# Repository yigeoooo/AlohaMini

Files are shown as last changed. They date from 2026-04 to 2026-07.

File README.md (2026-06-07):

# AlohaMini2
 

AlohaMini2 is a dual-arm mobile robot with a motorized vertical lift — a major generational upgrade over AlohaMini1 while keeping the self-build BOM under $1,000.  

Fully 3D-printable on a Bambu P2S, built for embodied AI research, and priced for anyone serious about real-world manipulation.

> Assemble at home in ~120 minutes. Train or deploy with LeRobot.

## Updates

- [2026-06-06] AlohaMini2 released — 70 kg base load, 30 kg lift, 1 kg arm payload, 6+1 DoF, 52 cm reach, under $1,000 self-build BOM
- [2026-02-26] Fine-tuning and deployment guide for Pi 0.5 on AlohaMini (`examples/pi0.5_openpi`)
- [2025-12-18] URDF and simulation assets available (`AlohaMini1/simulation/src/Aloha/`)
- [2025-11-27] STEP (CAD) files available (`AlohaMini1/hardware/mobile_base/step/`)

## What's New in AlohaMini2

### Architecture

| | AlohaMini | AlohaMini2 |
|---|---|---|
| Arm system | [SO-ARM100 / SO-ARM101](https://github.com/TheRobotStudio/SO-ARM100) | [AM-ARM200](https://github.com/liyiteng/AM-ARM) |
| Mobile base system | [mobile_base1](AlohaMini1/hardware/mobile_base/) | [mobile_base2](AlohaMini2/hardware/mobile_base2/) |
| Printer requirement | Large-format FDM (>= 380 mm bed) | Bambu P2S (consumer-grade) |

### Performance

| | AlohaMini | AlohaMini2 |
|---|---|---|
| Base max load | 10 kg | 70 kg  |
| Lift capacity | 5 kg | 30 kg |
| Lift stability | Standard | Significantly reinforced |
| Arm payload | 0.3 kg | 1 kg |
| Arm reach | 40 cm | 52 cm |
| Arm DoF | 5+1 | 6+1 |
| Cameras | 5 | 5 (forward, backward, chest, dual wrist) |

AlohaMini2 is LeRobot-ready out of the box and remains fully open-source — hardware CAD, URDF, and software included.

## Gallery

<p align="center">
  
</p>

## Bill of Materials (BOM)

> This BOM lists only the robot's major components, excluding the leader arm.

| Component | Model / Notes | Qty | Unit Price (USD) |
|---|---|-----|---|
| Servo — standard | Feetech STS-3215 (12V, follower arms + base) | 11 | ~$16 |
| Servo — high-torque | Feetech STS-3095 (12V 95 kg·cm, lift + arm power joints) | 7 | ~$50 |
| Bus servo controllers | Waveshare | 2 | ~$5 |
| Compute | Raspberry Pi 5 (2 GB) | 1 | ~$93 |
| Cameras | 720p USB, 2.4 mm focal length | 5 | ~$17 |
| Omni wheels | 127 mm (74A) | 3 | ~$40 |
| Battery 12V | 11200 mAh Li-ion | 2 | ~$16 |
| Frame | 3D-printed on Bambu P2S | — | ~6 kg filament |
| **Total** | — | — | **~$950** |

> Full BOM with CN/US buy links: **[AlohaMini2/docs/BOM.md](AlohaMini2/docs/BOM.md)**  
> Compute can be swapped for Jetson Orin Nano or any SBC with USB 3.0.  

## Quick Start

1. **BOM** — review the component list and source parts  
   See **[Bill of Materials](AlohaMini2/docs/BOM.md)**

2. **3D Printing** — print all structural parts (~6 kg filament, Bambu P2S)  
   See **[Print Guide](AlohaMini2/docs/print_guide.md)**

3. **Assembly** — build in ~120 minutes (arms pre-assembled)  
   See **[Assembly Guide](AlohaMini2/docs/assembly_guide.md)**

4. **Software setup & teleoperation** — install, connect, control  
   See **[Software Guide](software)**

## Product Line

| Model | Servo System | Chassis | Best For | Official Store (CN) |
|---|---|---|---|---|
| **AlohaMini2** | STS-3215 standard servos | 3D-printed base | Self-build research and development | [Taobao](https://item.taobao.com/item.htm?abbucket=9&id=1015799132286) |
| **AlohaMini2 Pro** | STS-3250 industrial-grade servos | Metal-reinforced base | Higher-duty research and lab use | [Taobao](https://item.taobao.com/item.htm?abbucket=9&id=1015799132286) |

## Contact

Email: liyiteng+github@gmail.com  
WeChat: liyiteng  
Videos & tutorials: Bilibili / YouTube / TikTok

## Team

AlohaMini is created by **Li Yiteng** and **Wu Zhiyong**.

## Acknowledgements

Thanks to the open robotics community:  
**ALOHA · LeKiwi · SO-ARM100 · SO-ARM100-Track-Axis · Pi-0.5 · LeRobot · Hugging Face**

## Support AlohaMini

If you find this project useful:
- Star the repo
- Follow for updates
- Join the community on Discord

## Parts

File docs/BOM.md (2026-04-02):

# Bill of Materials

AlohaMini follows the same architecture and terminology as LeKiwi, consisting of a Client side and a Host side.

- The Client handles computation and control.
- The Host executes commands and returns observations.

This is also commonly referred to as PC side vs. Remote side, and both naming conventions are equivalent.

AlohaMini’s Client hardware includes the mobile base and two follower arms. The arms directly reuse the SO-ARM100 design. Therefore, if you already have two SO-ARM100 arms, you only need to assemble the mobile base. Communication between the mobile base, arms, and Raspberry Pi 5 uses the same bus-servo communication system, and the build guide will explain the wiring in detail.

On AlohaMini, the Host side consists of a PC workstation and leader arms. VR controllers or other devices can also replace the leader arms, and we will release compatible controller kits soon. For beginners, we recommend starting with leader-arm teleoperation.

*Note: Table clamp, screwdriver set, soldering iron, and other common tools can be sourced as needed and are not listed in the tables below.*

## Mobile base 

| Item | Model / Notes | Qty | Unit Cost (US) | Buy (US) | Unit Cost (CN) | Buy (CN) |
|---|---|-----|---|---|---|---|
| Servo motor | Feetech / 12V 1/345 Gear(STS3215-C018)| 4 | $13.89 | [Alibaba](https://www.alibaba.com/product-detail/Feetech-12V-1-345-STS3215-C018_1601637205886.html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) | ¥110 | [taobao](https://item.taobao.com/item.htm?id=996544351583&spm=a213gs.v2success.0.0.73c04831naDrHP) |
| Omni wheel | 4″ (≈100 mm) | 3 | $47 | [Amazon](https://www.amazon.com/Replacement-Plastic-Directional-Accessories-Platform/dp/B0F9W6QX5M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) | ¥135 | [pinduoduo](https://mobile.yangkeduo.com/goods.html?ps=kKWPC7xuzw) |
| USB camera | 720p focal length 2.4 mm, 36×36 mm form factor | 3 | — | Amazon | ¥125 | [taobao](https://item.taobao.com/item.htm?id=666278411821) |
| (optional) Bearing | 12×18×4 mm (ID × OD × W) — wheel axle bearing | 3 | — | Amazon | ¥6 | [tmall](https://detail.tmall.com/item.htm?id=824704356695) |
| Bearing | 4×13×5 mm (ID × OD × W) — lift axis bearing | 8 | — | Amazon | ¥3 | [taobao](https://item.taobao.com/item.htm?id=565418362178) |
| M2×12 Phillips screw | For camera mounts (OB_T_Camera_Mount.stl, OB_Top_Camera_Mount) | 12 | — | — | — | — |
| M3×12 hex socket screw | Total 36 pcs (Servo Mount×24 ,Side Panel×12 ) | 36 | — | — | — | — |
| M3×18 hex socket screw | For OB_Chassis_Wheel_Axle_Connector.stl | 12 | — | — | — | — |
| M3×30 hex socket screw | For OB_T_Connector_Right/Left.stl | 8 | — | — | — | — |
| M3 hex nut | For OB_T_Connector_Right/Left.stl | 8 | — | — | — | — |
| M3x5x4 heat-set insert | Total 36 pcs (Servo Mount×24, Side Panel×12) | 36 | — | Amazon | ¥5 | [taobao](https://item.taobao.com/item.htm?id=809241671998) |
| M4×12 hex socket screw | Total 20 pcs (Bearing Cover×12, Z-axis Servo Mount×8) | 20 | — | Amazon | — | — |
| M4x6x5 heat-set insert | For OB_Chassis_Bearing_Cover.stl | 12 | — | Amazon | ¥4 | [taobao](https://item.taobao.com/item.htm?id=809241671998) |
| Adhesive | Epoxy (strongly recommended) / double-sided tape — cable retention & structural bonding | 1 | — | Amazon | ¥12 | [jd](https://item.jd.com/100141557259.html) |
| Servo extension cable | SCS 3-pin, 90 cm | 2 | — | [Alibaba](https://www.alibaba.com/product-detail/3P-5264-Interface-Bus-Actuator-Connection_1601635790774.html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) | ¥3 | [taobao](https://item.taobao.com/item.htm?id=616460581906) |
| Battery | 12 V Li-ion pack with 5521 barrel jack (male & female); one pack for the Raspberry Pi 5, the other for the mobile base and follower arms.| 2 | $43 | [Amazon](https://www.amazon.com/KBT-Rechargeable-Connector-Replacement-Security/dp/B0C242DYT1/ref=sr_1_2_sspa?th=1) | ¥130 | [taobao](https://item.taobao.com/item.htm?id=890828103056) |
| USB Type-C cable | Only for testing the mobile base | 1 | $10 | [Amazon](https://www.amazon.com/Charging-etguuds-Charger-Braided-Compatible/dp/B0B8NWLLW2/?th=1) | ¥20 | [tmall](https://detail.tmall.com/item.htm?id=754024805047) |
| Waveshare Bus Servo Controller | Only for testing the mobile base | 1 | $13 | [Amazon](https://www.amazon.com/Waveshare-Integrates-Control-Circuit-Supports/dp/B0CTMM4LWK/) | ¥27 | [tmall](https://detail.tmall.com/item.htm?id=738817173460) |
| 3D-printed parts | PLA/PETG/ABS (files in /hardware/mobile_base/stl) | ~4 kg filament | — | — | — | — |

**3D Printing Parts List:**
- OB_Chassis_Bearing_Cover x3
- OB_Chassis_Servo_Mount x3
- OB_Chassis_Side_Panel x3
- OB_Chassis_Wheel_Axle_Connector x3
- OB_Chassis_Wheel_Guard x3
- OB_Top_Camera_Back_Cover x2
- OB_Chassis_Shaft_Sleeve_12_24 x3
- O_Chassis_Dowel_Pin_12_37 x3
- All other files x1

Note：
All other parts — including the lift mechanism — can be printed on a standard 3D printer. Only the chassis is special, as it requires a build volume of at least 385 × 345 × 64 mm. We recommend choosing a machine with around 400 × 360 × 100 mm or larger. Due to its size, the chassis may need to be outsourced for printing.

### What the Base Can Do

With only the components above, you can assemble the **mobile base** and control:

- movement  
- vertical lift  

Use the following commands to control the base:
```bash
python examples/debug/wheels.py \
   --port /dev/ttyACM0

python examples/debug/axis.py \
   --port /dev/ttyACM0
```

Use W/S/A/D to drive the base, and U/J to raise or lower the lift — all directly from your PC, without installing any single-board computer on the robot.

More details will be provided in the software setup section.

Effect after assembly:

Assembled AlohaMini mobile base
### Standalone Mode (Optional)

If you prefer the base to operate as an **independent host system** (Wi‑Fi, untethered), add:

| Item | Model / Notes | Qty | Unit Cost (US) | Buy (US) | Unit Cost (CN) | Buy (CN) |
|---|---|-----|---|---|---|---|
| Compute board | Raspberry Pi 5 (≥ 2GB RAM) | 1 | $80 | [Adafruit](https://www.adafruit.com/product/5812) | ¥600 | [taobao](https://item.taobao.com/item.htm?id=688878446695) |
| DC converter | 12V → 5V / 5A buck converter | 1 | $13 | [Amazon](https://www.amazon.com/Klnuoxj-Converter-Interface-Waterproof-Compatible/dp/B0CRVW7N2J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) | ¥75 | [taobao](https://item.taobao.com/item.htm?id=800698078303) |
| Monitor | 7-inch HD IPS HDMI interface + touch + Type C power supply | 1 | — | Amazon | ¥291 | [taobao](https://item.taobao.com/item.htm?id=592070943040) |

## Follower Arms
| Item | Model / Notes | Qty | Unit Cost (US) | Buy (US) | Unit Cost (CN) | Buy (CN) |
|---|---|-----|---|---|---|---|
| Servo motor | Feetech / 12V 1/345 Gear(STS3215-C018) | 12 | $13.89 | [Alibaba](https://www.alibaba.com/product-detail/Feetech-12V-1-345-STS3215-C018_1601637205886.html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) | ¥110 | [taobao](https://item.taobao.com/item.htm?id=996544351583&spm=a213gs.v2success.0.0.73c04831naDrHP) |
| Waveshare Bus Servo Controller | For connecting to the Raspberry Pi 5 | 2 | $13 | [Amazon](amazon.com/Waveshare-Integrates-Control-Circuit-Supports/dp/B0CTMM4LWK/) | ¥27 | [tmall](https://detail.tmall.com/item.htm?id=738817173460) |
| USB camera | 720p focal length 3.8 mm, 32×32 mm form factor | 2 | — | Amazon | ¥103 | [taobao](https://item.taobao.com/item.htm?id=590682120464) |
| 1-to-2 DC splitter cable | 30 cm, 5521 connector — for powering the arms | 1 | — | Amazon | ¥5 | [taobao](https://item.taobao.com/item.htm?id=594921965049) |
| DC extension cable | 1.5 m, 5521 connector — for powering the arms | 2 | — | Amazon | ¥2.50 | [taobao](https://item.taobao.com/item.htm?id=43628177900) |
| USB Type-C cable | For connecting to the Raspberry Pi 5 | 2 | $10 | [Amazon](https://www.amazon.com/Charging-etguuds-Charger-Braided-Compatible/dp/B0B8NWLLW2/?th=1) | ¥20 | [tmall](https://detail.tmall.com/item.htm?id=754024805047) |
| 3D-printed parts | PLA/PETG/ABS (files in /hardware/arms/stl) | 1 set | — | — | — | — |

**3D Printing Parts List:**
- All "D_*.stl" files: x2
- All "F_*.stl" files: x2

For detailed printing instructions, refer to the [SO-ARM100 project README](https://github.com/TheRobotStudio/SO-ARM100)

## Leader Arms
> **Note:** The official SO-ARM100 design uses three different gear ratios (1/147, 1/191, 1/345) for optimal performance. However, our testing shows that using a single gear ratio (1/147) provides excellent user experience and significantly simplifies assembly. The BOM below reflects this simplified configuration.

| Item | Model / Notes | Qty | Unit Cost (US) | Buy (US) | Unit Cost (CN) | Buy (CN) |
|---|---|-----|---|---|---|---|
| Servo motor | Feetech / 7.4V 1/147 Gear(STS3215-C046) | 12 | $13.89 | [Alibaba](https://www.alibaba.com/product-detail/Feetech-STS3215-Servos-Feetech-7-4V_1601636218844.html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) | ¥99 | [taobao](https://item.taobao.com/item.htm?id=996544351583&spm=a213gs.v2success.0.0.73c04831naDrHP) |
| Waveshare Bus Servo Controller | For connecting to the PC | 2 | $13 | [Amazon](https://www.amazon.com/Waveshare-Integrates-Control-Circuit-Supports/dp/B0CTMM4LWK/) | ¥27 | [tmall](https://detail.tmall.com/item.htm?id=738817173460) |
| Battery | 5V Li-ion pack (5600mAh, DC 5521 connector) | 1 | — | Amazon | ¥30 | [taobao](https://item.taobao.com/item.htm?id=765749120668) |
| 1-to-2 DC splitter cable | 70 cm — for powering the arms | 1 | — | Amazon | ¥5 | [taobao](https://item.taobao.com/item.htm?id=594921965049) |
| USB Type-C cable | For connecting to the PC | 2 | $10 | [Amazon](https://www.amazon.com/Charging-etguuds-Charger-Braided-Compatible/dp/B0B8NWLLW2/?th=1) | ¥20 | [tmall](https://detail.tmall.com/item.htm?id=754024805047) |
| 3D-printed parts | PLA/PETG/ABS (files in /hardware/arms/stl) | 1 set | — | — | — | — |

**3D Printing Parts List:**
- All "D_*.stl" files: x2
- All "L_*.stl" files: x2

For detailed printing instructions, refer to the [SO-ARM100 project README](https://github.com/TheRobotStudio/SO-ARM100)

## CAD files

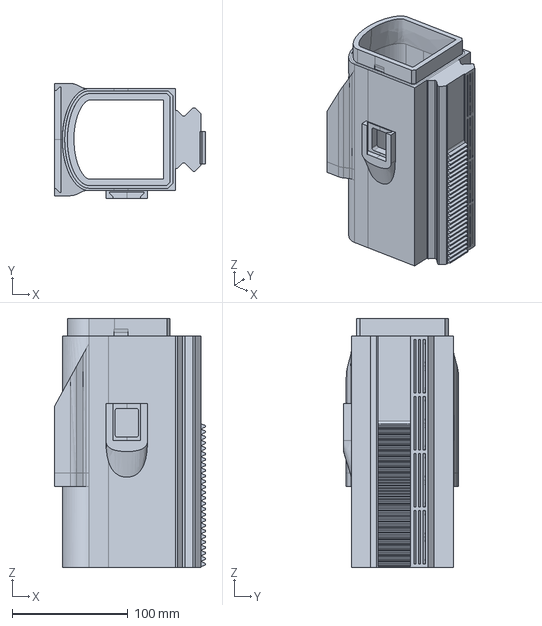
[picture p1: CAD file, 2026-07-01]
AlohaMini2/hardware/mobile_base2/stp/OB_Main_Assembly_Post1.stp
130.7 x 99.4 x 215.0 mm

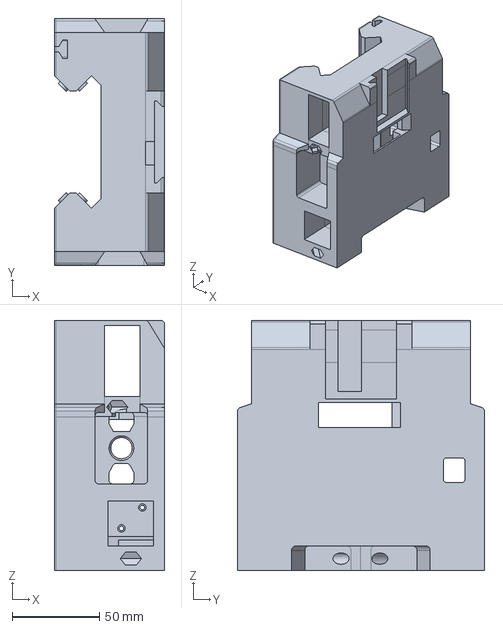
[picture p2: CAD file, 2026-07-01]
AlohaMini2/hardware/mobile_base2/stp/OB_T_Connector_Middle.stp
63.2 x 141.7 x 143.6 mm

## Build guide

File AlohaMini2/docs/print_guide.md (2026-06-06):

# AlohaMini2 Print Guide

AlohaMini2 structural parts can be printed with PLA, PETG, ABS, or similar FDM materials. The parts are designed for a Bambu P2S-class printer.

## Recommended Settings

| Setting | Recommendation |
|---|---|
| Wall loops | 4-6 |
| Infill | 15-25% |
| Support | Enable where required by the slicer |

For the best strength, use **6 wall loops** on load-bearing parts.

## Printed Parts

Print the STL files from:

```text
AlohaMini2/hardware/mobile_base2/stl/
```

Unless listed otherwise, each STL file is printed once.

| STL file | Qty | Notes |
|---|---:|---|
| `O_Chassis_Dowel_Pin_12_80.stl` | 3 | Printed substitute for chassis steel pins |
| `O_Main_Assembly_Post4.stl` | 1 |  |
| `O_POST4_Connector_Base.stl` | 1 |  |
| `O_T_Connector_Cross_Bar.stl` | 1 | Printed substitute for the aluminum T-frame |
| `O_T_Connector_Dowel_Pin_12_25.stl` | 1 | Printed substitute for the lift-axis steel pin |
| `OB_Buck_Converter_Mount.stl` | 1 |  |
| `OB_Chassis_Bearing_Cover.stl` | 3 |  |
| `OB_Chassis_Frame_Joiner.stl` | 3 |  |
| `OB_Chassis_Locking_Wedge.stl` | 3 |  |
| `OB_Chassis_Segment_1of3_PrintOptimized.stl` | 3 | Recommended chassis segment |
| `OB_Chassis_Wheel_Axle_Connector.stl` | 3 |  |
| `OB_Main_Assembly_Post1.stl` | 1 |  |
| `OB_Main_Assembly_Post2.stl` | 1 |  |
| `OB_Main_Assembly_Post3.stl` | 1 |  |
| `OB_Main_Monitor_Connector.stl` | 1 |  |
| `OB_POST4_Mount_Adapter.stl` | 1 |  |
| `OB_POST4_RPi_Mount.stl` | 1 |  |
| `OB_T_Camera_Mount.stl` | 1 |  |
| `OB_T_Connector_Left.stl` | 1 |  |
| `OB_T_Connector_Middle.stl` | 1 |  |
| `OB_T_Connector_Right.stl` | 1 |  |
| `OB_Top_Camera_Back_Cover.stl` | 2 |  |
| `OB_Top_Camera_Mount.stl` | 1 |  |
| `OB_Z_Axis_Servo_Gear.stl` | 1 |  |

## Material Notes

| Material | Notes |
|---|---|
| PLA | Easiest to print, but lower strength and heat resistance. Good for general test builds. |
| PETG | Tougher than PLA, but stringier and more prone to rack/gear tooth adhesion. Use PLA or dedicated support material for support interfaces when possible. |
| ABS | Stronger and more heat-resistant, but more likely to warp. Use an enclosed printer, such as X2D, and control chamber temperature. |

## Chassis Printing

The chassis segments are large and can warp during printing. For the chassis, use the print-optimized STL when available:

```text
OB_Chassis_Segment_1of3_PrintOptimized.stl
```

## Printed Substitutes

If the BOM-listed aluminum extrusion for the T-frame or the chassis steel pins are not available, printed substitutes can be used. However, printed substitutes will significantly reduce structural strength. Use metal parts for the final build whenever possible.

## Bambu Studio Plate Layout

Use this Bambu Studio Prepare view as the print plate layout reference:

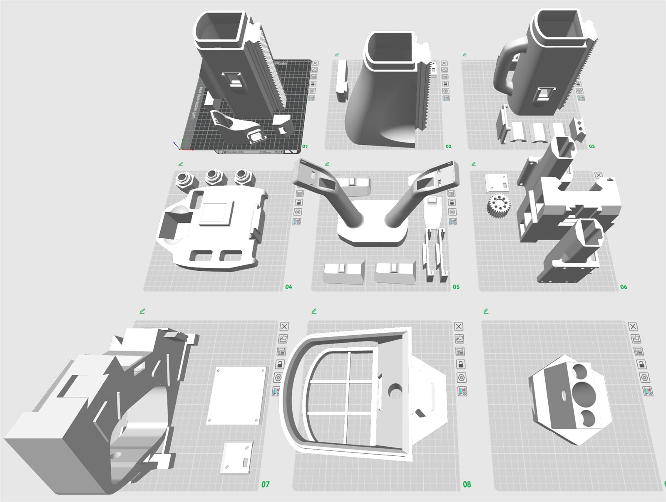
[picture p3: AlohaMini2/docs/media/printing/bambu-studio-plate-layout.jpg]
Bambu Studio print plate layout for AlohaMini2 parts


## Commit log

2026-06-06 fix: correct lift capacity in AlohaMini2 release update
2026-06-06 feat: add print guide
2026-06-07 fix: update BOM details
